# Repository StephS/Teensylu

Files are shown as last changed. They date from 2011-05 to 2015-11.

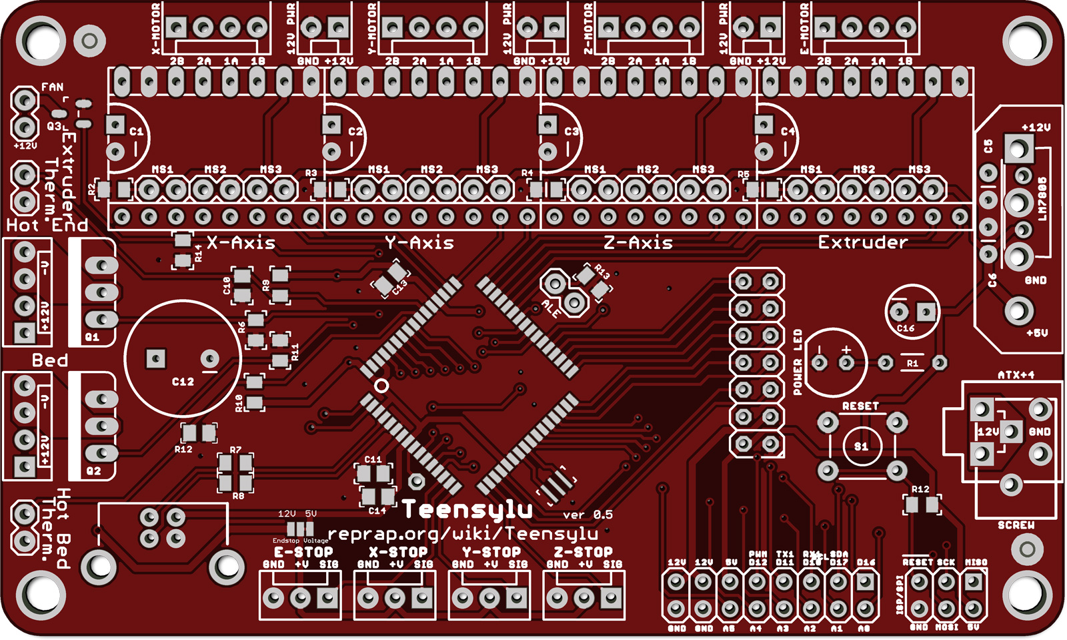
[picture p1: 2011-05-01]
teensylu-0.5/images/top.jpg

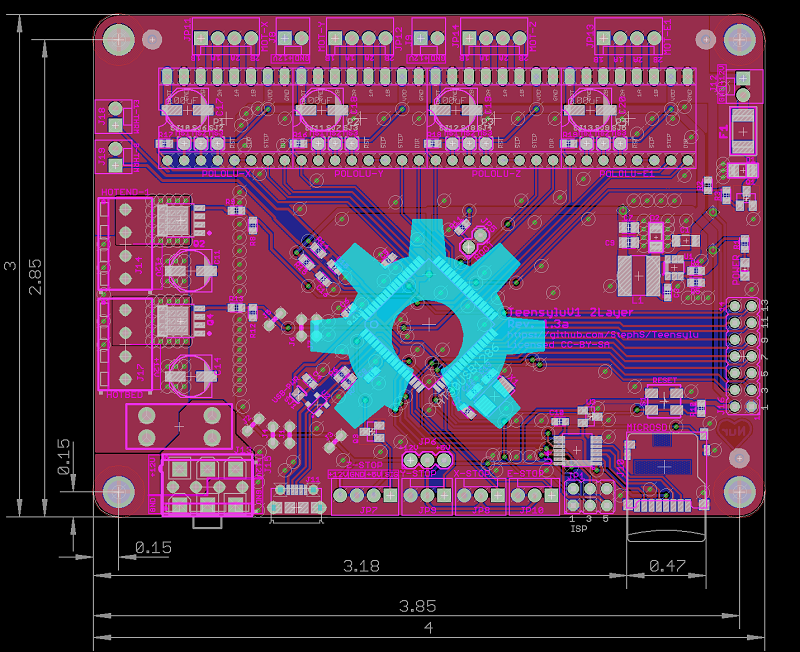
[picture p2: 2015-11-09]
TeensyluV1-2Layer/board.png

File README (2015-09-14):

UPDATE: TeensyluV1 is a complete redesign of the board. I have moved the power connector closer to the mosfets. Pins have changed! This new board is slightly larger than the older versions - It now matches the size of the Teensylu2
The hotend and bed connectors have changed to high power connectors. The main power connector can either be  screw connector, or a 6-Pin ATX-PCIE power connector. Please note the orientation of the connector and the polarity! Do not use the older 4 pin ATX connector!!!
It is highly recommended that this board is built using 2oz-in copper. Less than that may lead to board damage or FIRE!
I recommend a 15 Amp fuse in the mini-blade fuse holder.

I do not recommend using the older teensylu boards, get the TeensyluV1 board and use the added safety features.

I have decided to release 2 different versions of the board, The 2 Layer version, and 4 Layer version. The 4 layer version has greater power capacity due to uninterrupted power planes. The 2 layer version will be cheaper to manufacture. Functionally the boards are identical. I would prefer the 4 layer version, but I realize that COST is a major issue (up to 3 times the cost to manufacture 4 layer versus 2 layer).

As with all hobbiest electronics, there is a certain degree of risk involved. I had hoped that by making this project open source, that users would provide feedback and improvements to the design.
This has not happened.

Again, Use this board at your own risk!
I am releasing these designs without warranty or guarantee.

There is no such thing as a "Safe" 3d printer controller. Keep a smoke detector nearby and have a fire extinguisher handy. Do NOT the leave unattended. Disconnect from power source when not in use.

http://reprap.org/wiki/Teensylu

If you'd like to donate so I can buy the full version of Eagle, and make more cool stuff, please contact me through Google+ at https://plus.google.com/+StephanieS3D

Disclaimer:
These designs are provided without any warrenty, expressed or implied. This is a prototype designed for hobbiest use only.
Care should be taken during use and appropriate safety precautions taken.
The author is providing this item "as is". The author does not provide any warranty of the item whatsoever, whether express, implied, or statutory, including, but not limited to, any warranty of merchantability or fitness for a particular purpose or any warranty that the contents of the item will be error-free.
In no respect shall the author incur any liability for any damages, including, but limited to, direct, indirect, special, or consequential damages arising out of, resulting from, or any way connected to the use of the item, whether or not based upon warranty, contract, tort, or otherwise; whether or not injury was sustained by persons or property or otherwise; and whether or not loss was sustained from, or arose out of, the results of, the item, or any services that may be provided by the author.

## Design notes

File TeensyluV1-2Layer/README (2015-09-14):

Version 1.3 is ready for production, earlier versions should not be used.
This version is a 2 Layer board designed for low cost manufacturing. A 4 Layer board is also available.
It is required that the top and bottom layers be 2oz/in.
24v power supply should be possible, please note to use a 24v heat bed, hotend, and fans or else damage or FIRE can occur.

Assembly notes:
J1-J7 are 22ga Solid core wire jumpers at 0.1" spacing. Do not attempt to stuff with headers.
J13 and J15 occupy the same space. Choose an appropriate header for the target system.

Please see TeensyluV1_Pin_Mapping.txt for the correct pin mapping using the teensyduino library. Analog pins should use the analog pin reference.

The BOM is included. Please use parts of the same or higher ratings.

If you'd like to donate so I can buy the full version of Eagle, and make more cool stuff, please contact me through Google+ at https://plus.google.com/+StephanieS3D

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

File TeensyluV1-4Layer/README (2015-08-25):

Version 1.2 is ready for production, earlier versions should not be used.
This latest version of the board utilizes 4 layers. This is to improve the current capacity of the power planes.
It is recommended that the top and bottom layers be 2oz/in.
24v power supply should be possible, please note to use a 24v heat bed, hotend, and fans or else damage or FIRE can occur.

Please see TeensyluV1_Pin_Map.htm for the correct pin mapping using the teensyduino library. Analog pins should use the analog pin reference.

The BOM is included. Please use parts of the same or higher ratings.

If you'd like to donate so I can buy the full version of Eagle, and make more cool stuff, please contact me through Google+ at https://plus.google.com/+StephanieS3D

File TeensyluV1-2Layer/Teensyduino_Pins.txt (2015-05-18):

Pin #	PORT
0	PD0
1	PD1
2	PD2
3	PD3
4	PD4
5	PD5
6	PD6
7	PD7
8	PE0
9	PE1
10	PC0
11	PC1
12	PC2
13	PC3
14	PC4
15	PC5
16	PC6
17	PC7
18	PE6
19	PE7
20	PB0
21	PB1
22	PB2
23	PB3
24	PB4
25	PB5
26	PB6
27	PB7
28	PA0
29	PA1
30	PA2
31	PA3
32	PA4
33	PA5
34	PA6
35	PA7
36	PE4
37	PE5
38	PF0
39	PF1
40	PF2
41	PF3
42	PF4
43	PF5
44	PF6
45	PF7

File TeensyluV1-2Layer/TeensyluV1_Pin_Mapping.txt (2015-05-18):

Package Pin Number	Pin Name	Teensyduino Pin Number	Connected NET	Description
1	PE6	18	Z-STOP	Z Endstop or Z probe input
2	PE7	19	PE7	Not Connected
9	PE3		PE3	Not Connected
10	PB0	20	SDCS	SDCS
11	PB1	21	SCLK	SCLK
12	PB2	22	MOSI	MOSI
13	PB3	23	MISO	MISO
14	PB4	24	PB4	Extension Header PIN 5
15	PB5	25	Y-STOP	Y Endstop
16	PB6	26	X-STOP	X Endstop
17	PB7	27	SCDCD	SD Card Detect
18	PE4	36	E-STOP	E Endstop
19	PE5	37	PE5	Extension Header PIN 4
25	PD0	0	PD0-SCL	Extension Header PIN 6
26	PD1	1	PD1-SDA	Extension Header PIN 7
27	PD2	2	PD2-RX1	Extension Header PIN 8
28	PD3	3	PD3-TX1	Extension Header PIN 9
29	PD4	4	PD4	Extension Header PIN 10
30	PD5	5	PD5	Extension Header PIN 11
31	PD6	6	PD6	Extension Header PIN 12
32	PD7	7	PD7	Extension Header PIN 13
33	PE0	8	E2-STEP	Not Connected
34	PE1	9	E2-DIR	Not Connected
35	PC0	10	!E2-ENABLE	Not Connected
36	PC1	11	E1-DIR	1st Extruder STEP pin
37	PC2	12	E1-STEP	1st Extruder DIR pin
38	PC3	13	!E1-ENABLE	1st Extruder ENABLE pin
39	PC4	14	!HOTBED	Hot Bed Mosfet control pin
40	PC5	15	!HOTEND-1	Hot End 1 Mosfet control pin
41	PC6	16	!PWM-FAN	Fan Mosfet control pin
42	PC7	17	Z-DIR	Z Axis STEP pin
43	PE2		PE2	Boot Mode pin
44	PA7	35	Z-STEP	Z Axis DIR pin
45	PA6	34	!Z-ENABLE	Z Axis ENABLE pin
46	PA5	33	Y-DIR	Y Axis STEP pin
47	PA4	32	Y-STEP	Y Axis DIR pin
48	PA3	31	!Y-ENABLE	Y Axis ENABLE pin
49	PA2	30	X-DIR	X Axis STEP pin
50	PA1	29	X-STEP	X Axis DIR pin
51	PA0	28	!X-ENABLE	X Axis ENABLE pin
54	PF7	45	A7	Extension Header PIN 14
55	PF6	44	A6	Not Connected
56	PF5	43	A5	Not Connected
57	PF4	42	A4	Not Connected
58	PF3	41	!HOTEND-2	Not Connected
59	PF2	40	E2-THERM	Not Connected
60	PF1	39	E1-THERM	Hot End 1 thermistor input pin
61	PF0	38	B-THERM	Hot Bed thermistor input pin

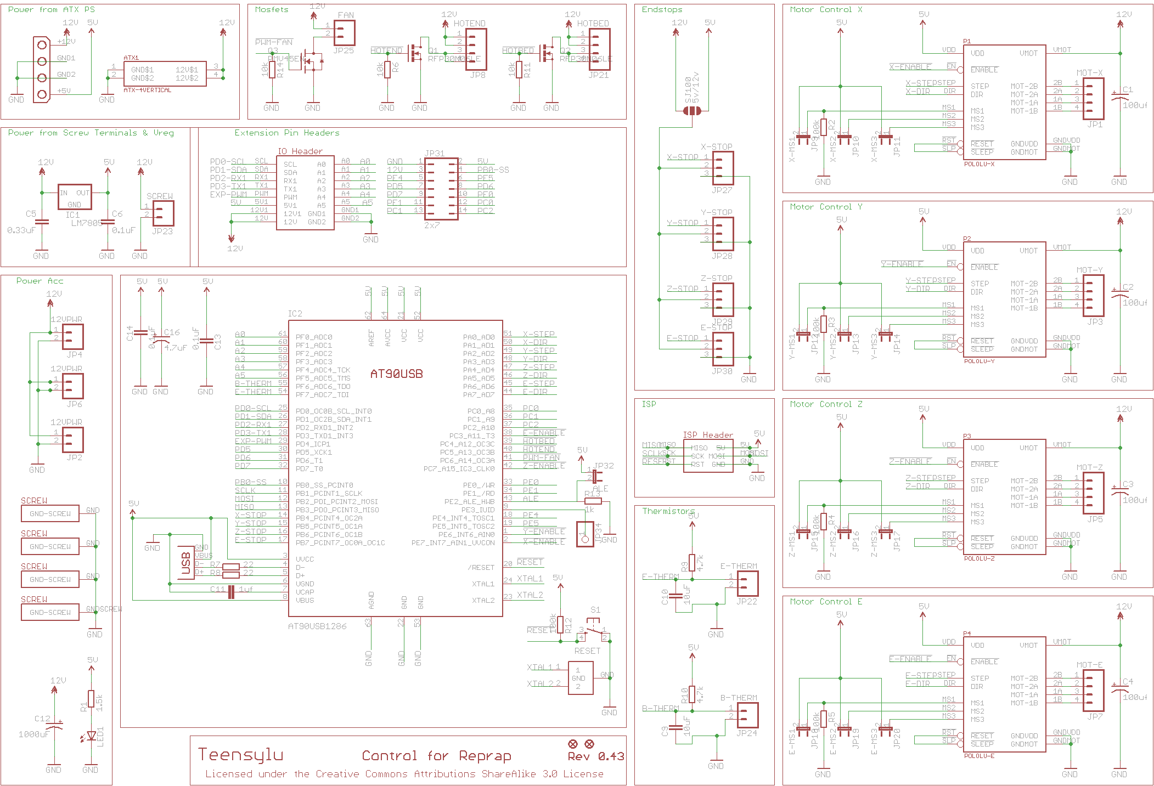
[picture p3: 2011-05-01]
teensylu-0.4.3/Schematic.png

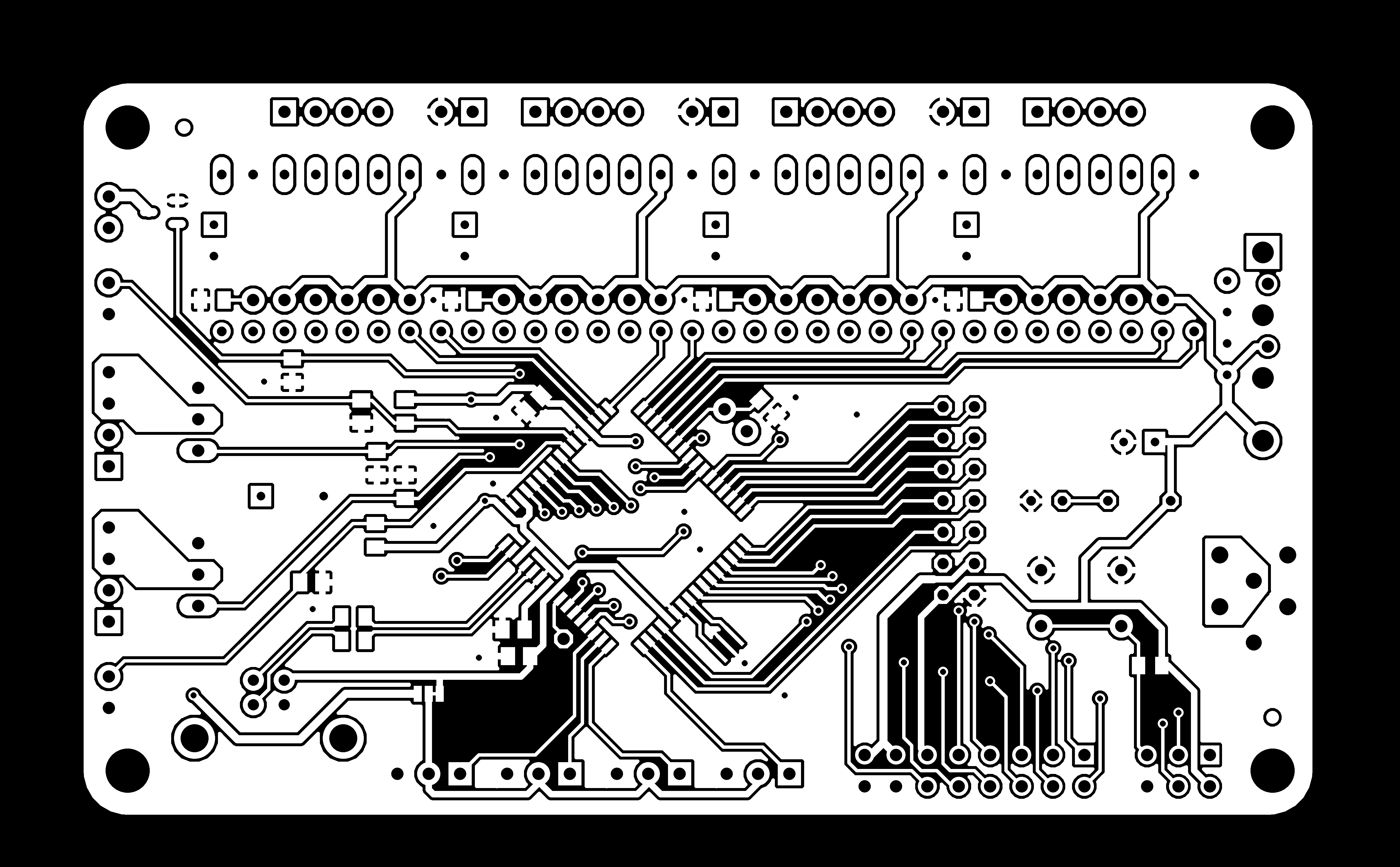
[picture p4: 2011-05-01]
teensylu-0.5/images/eagle_top.png

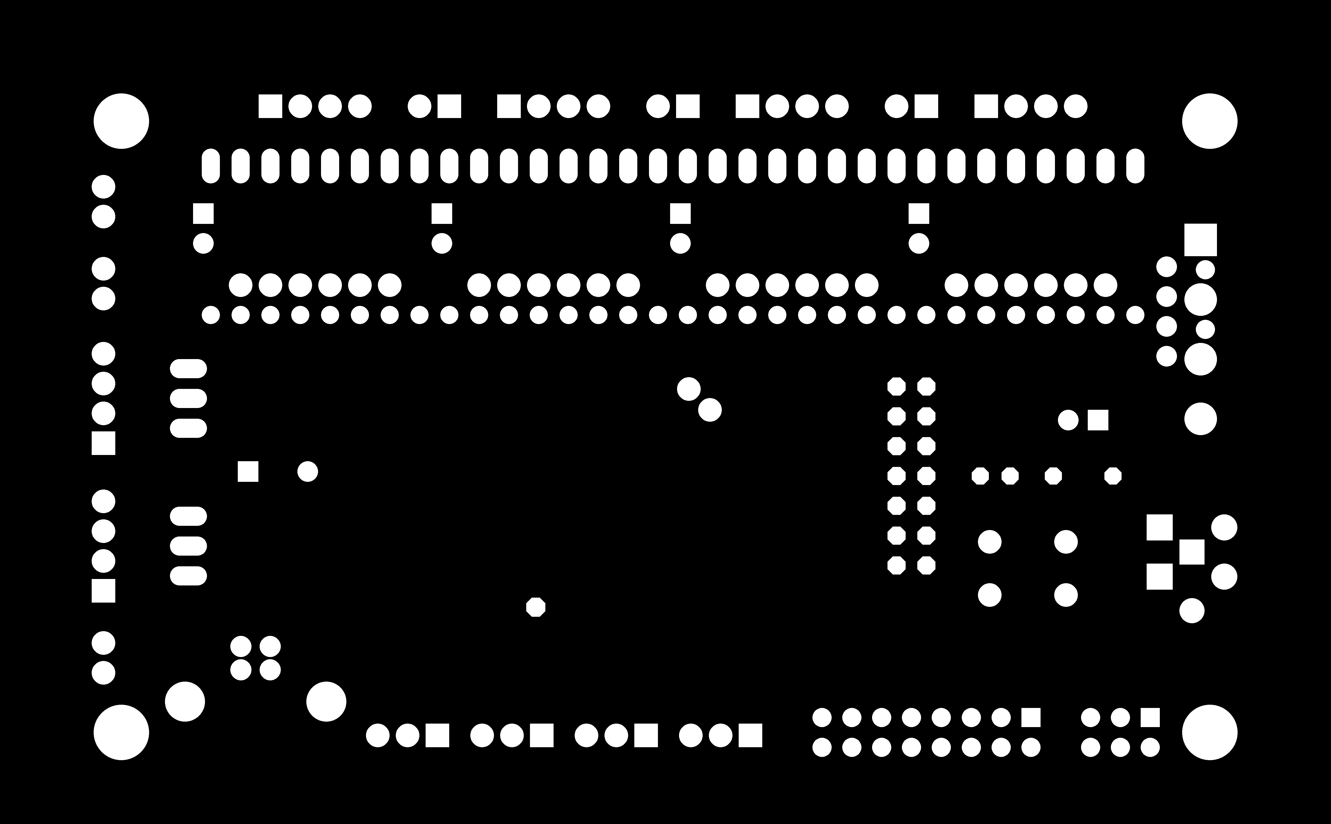
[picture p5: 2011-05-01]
teensylu-0.5/images/eagle_bottom_mask.png

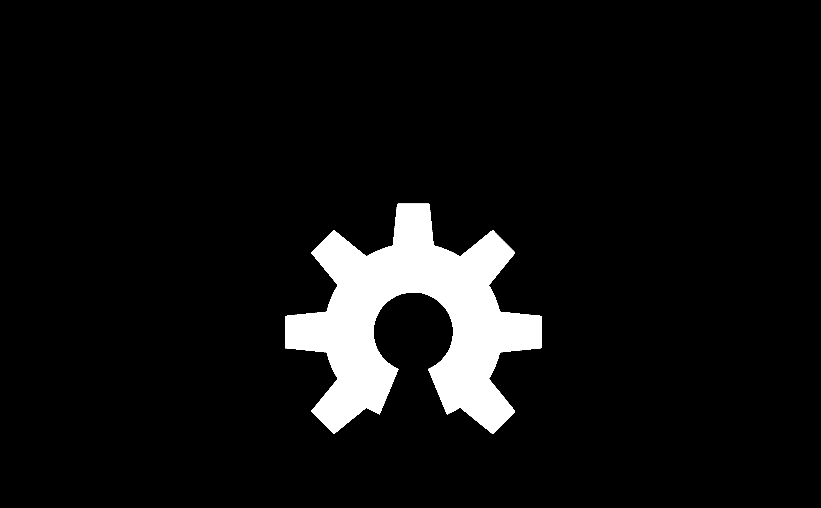
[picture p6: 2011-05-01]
teensylu-0.5/images/eagle_bottom_silk.png

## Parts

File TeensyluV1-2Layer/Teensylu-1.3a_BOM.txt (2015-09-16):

Part   Value                 Device                     Package             Description                                                                   CURRENT DCR   DESCRIPTION                               ESR    INDUCTANCE IRMS MANUFACTURER            MANUFACTURER_PART_NUMBER      NOTES                                                                       RDS_ON  REVERSE_VOLTAGE TOLERANCE VDC VGS   VOLTAGE VOLTAGE_OUTPUT
C1     4.7uF                 CAPACITOR_1206             CAPC3215X168N                                                                                                                                                                    Yaiyo Yuden             UMK316AB7475KL-T                                                                                                                  10%       50v                             
C2     0.1uF                 CAPACITOR_0603             CAPC1608X92N                                                                                                                                                                     Murata                  GRM188R71C104KA01D                                                                                                                10%       16V                             
C3     0.1uF                 CAPACITOR_0603             CAPC1608X92N                                                                                                                                                                     Samsung                 CL10B104KB8NNNC                                                                                                                   10%       50V                             
C4     0.1uF                 CAPACITOR_0603             CAPC1608X92N                                                                                                                                                                     Murata                  GRM188R71C104KA01D                                                                                                                10%       16V                             
C5     0.1uF                 CAPACITOR_0603             CAPC1608X92N                                                                                                                                                                     Murata                  GRM188R71C104KA01D                                                                                                                10%       16V                             
C6     0.1uF                 CAPACITOR_0603             CAPC1608X92N                                                                                                                                                                     Murata                  GRM188R71C104KA01D                                                                                                                10%       16V                             
C7     10uF                  CAPACITOR_0805             CAPC2012X145AN                                                                                                                                            0.0030                 Murata                  GRM21BR71A106KE51L                                                                                                                10%       10v                             
C8     1uF                   CAPACITOR_0603             CAPC1608X92N                                                                                                                                                                     Samsung                 CL10A105MO8NNNC                                                                                                                   20%       16V                             
C9     10uF                  CAPACITOR_0805             CAPC2012X145AN                                                                                                                                            0.0030                 Murata                  GRM21BR71A106KE51L                                                                                                                10%       10v                             
C10    10uF                  CAPACITOR_0603             CAPC1608X92N                                                                                                                                                                     Murata                  GRM188R61C106MA73D                                                                                                                20%       16V                             
C11    100uF                 CPOL-USD                   PANASONIC_D         POLARIZED CAPACITOR, American symbol                                                                                                                         Panasonic               EEE-FTH101XAP                                                                                                                     20%       50v                             
C12    10pF                  CAPACITOR_0603             CAPC1608X92N                                                                                                                                                                     Samsung                 CL10C100JB8NCNC                                                                                                                   5%        50V                             
C13    10pF                  CAPACITOR_0603             CAPC1608X92N                                                                                                                                                                     Samsung                 CL10C100JB8NCNC                                                                                                                   5%        50V                             
C14    100uF                 CPOL-USD                   PANASONIC_D         POLARIZED CAPACITOR, American symbol                                                                                                                         Panasonic               EEE-FTH101XAP                                                                                                                     20%       50v                             
C15    10uF                  CAPACITOR_0603             CAPC1608X92N                                                                                                                                                                     Murata                  GRM188R61C106MA73D                                                                                                                20%       16V                             
C16    10uF                  CAPACITOR_0603             CAPC1608X92N                                                                                                                                                                     Murata                  GRM188R61C106MA73D                                                                                                                20%       16V                             
C17    100uF                 CPOL-USD                   PANASONIC_D         POLARIZED CAPACITOR, American symbol                                                                                                                         Panasonic               EEE-FTH101XAP                                                                                                                     20%       50v                             
C18    100uF                 CPOL-USD                   PANASONIC_D         POLARIZED CAPACITOR, American symbol                                                                                                                         Panasonic               EEE-FTH101XAP                                                                                                                     20%       50v                             
C19    100uF                 CPOL-USD                   PANASONIC_D         POLARIZED CAPACITOR, American symbol                                                                                                                         Panasonic               EEE-FTH101XAP                                                                                                                     20%       50v                             
C20    100uF                 CPOL-USD                   PANASONIC_D         POLARIZED CAPACITOR, American symbol                                                                                                                         Panasonic               EEE-FTH101XAP                                                                                                                     20%       50v                             
D1     SCH-DIODESOD123F      SCH-DIODESOD123F           SOD123F             Schottky Diodes                                                               1A                                                                             NXP Semiconductors      PMEG4010CEH,115                                                                                                   40V                                                       
D2     SCH-DIODESOD123F      SCH-DIODESOD123F           SOD123F             Schottky Diodes                                                               1A                                                                             NXP Semiconductors      PMEG4010CEH,115                                                                                                   40V                                                       
F1     MINISMDC050F1812      MINISMDC050F1812           MINISMDC                                                                                          0.5A                                                                           TE Connectivity         MINISMDC050F-2                                                                                                                                                              
F2     MINI-FUSEMINI-FUSE    MINI-FUSEMINI-FUSE         MINI_FUSE                                                                                         15A                                                                            Keystone                3568                                                                                                                                                                        
J1     22ga                  WIRE_JUMPER-0.1            WJ_01_08            A wire jumper.  This component lets you give the same net two different names               22ga jumper wire                                                 N/A                     N/A                                                                                                                                                                         
J2     22ga                  WIRE_JUMPER-0.1            WJ_01_08            A wire jumper.  This component lets you give the same net two different names               22ga jumper wire                                                 N/A                     N/A                                                                                                                                                                         
J3     22ga                  WIRE_JUMPER-0.1            WJ_01_08            A wire jumper.  This component lets you give the same net two different names               22ga jumper wire                                                 N/A                     N/A                                                                                                                                                                         
J4     22ga                  WIRE_JUMPER-0.1            WJ_01_08            A wire jumper.  This component lets you give the same net two different names               22ga jumper wire                                                 N/A                     N/A                                                                                                                                                                         
J5     22ga                  WIRE_JUMPER-0.1            WJ_01_08            A wire jumper.  This component lets you give the same net two different names               22ga jumper wire                                                 N/A                     N/A                                                                                                                                                                         
J6     22ga                  WIRE_JUMPER-0.1            WJ_01_08            A wire jumper.  This component lets you give the same net two different names               22ga jumper wire                                                 N/A                     N/A                                                                                                                                                                         
J7     22ga                  WIRE_JUMPER-0.1            WJ_01_08            A wire jumper.  This component lets you give the same net two different names               22ga jumper wire                                                 N/A                     N/A                                                                                                                                                                         
J8     M02POLAR              M02POLAR                   MOLEX-1X2           Header 2                                                                                    CONN HEADER 2POS .100 VERT TIN                                   Molex                   0022272021                    Can use alternative part for Right Angle. MFG: TE Connectivity PN: 640455-2                                                                   
J9     M02POLAR              M02POLAR                   MOLEX-1X2           Header 2                                                                                    CONN HEADER 2POS .100 VERT TIN                                   Molex                   0022272021                    Can use alternative part for Right Angle. MFG: TE Connectivity PN: 640455-2                                                                   
J10    MICROSD               MICROSD                    AMPHENOL-MICROSD                                                                                                CONN MICRO SD CARD PUSH-PULL R/A                                 Amphenol                114-00841-68                                                                                                                                                                
J11    USB-MICRO-PTH         USB-MICRO-PTH              USB-MICROB-PTH      USB Connectors                                                                                                                                               FCI                     10118194-0001LF                                                                                                                                                             
J12    M02POLAR              M02POLAR                   MOLEX-1X2           Header 2                                                                                    CONN HEADER 2POS .100 VERT TIN                                   Molex                   0022272021                    Can use alternative part for Right Angle. MFG: TE Connectivity PN: 640455-2                                                                   
J13    4P-TERM-BLOCK284391-4 4P-TERM-BLOCK284391-4      284391-4                                                                                          12A                                                                            TE Connectivity         284391-4                                                                                                                                                                    
J14    HOTEND-1              4P-TERM-BLOCK284391-4      284391-4                                                                                          12A                                                                            TE Connectivity         284391-4                                                                                                                                                                    
J15    39-29-3066            39-29-3066                 39-29-3066          Mini FIT connector 6 pol Without Snap-in peg                                                                                                                 Molex                   0039293066                                                                                                                                                                  
J16    2x7                   JP7Q                       JP7Q                JUMPER                                                                                      DIL VERTICAL PC TAIL PIN HEADER                                  Harwin                  M20-9980746                                                                                                                                                                 
J17    HOTBED                4P-TERM-BLOCK284391-4      284391-4                                                                                          12A                                                                            TE Connectivity         284391-4                                                                                                                                                                    
J18    M02POLAR              M02POLAR                   MOLEX-1X2           Header 2                                                                                    CONN HEADER 2POS .100 VERT TIN                                   Molex                   0022272021                    Can use alternative part for Right Angle. MFG: TE Connectivity PN: 640455-2                                                                   
J19    M02POLAR              M02POLAR                   MOLEX-1X2           Header 2                                                                                    CONN HEADER 2POS .100 VERT TIN                                   Molex                   0022272021                    Can use alternative part for Right Angle. MFG: TE Connectivity PN: 640455-2                                                                   
JP1    ISP                   PROGHEADER                 ISP                 JUMPER                                                                                                                                                                                                                                                                                                                                                           
JP2    FIDUCIAL1X2.5         FIDUCIAL1X2.5              FIDUCIAL-1X2.5      Fiducial Alignment Points                                                                                                                                                                                                                                                                                                                                        
JP3    FIDUCIAL1X2.5         FIDUCIAL1X2.5              FIDUCIAL-1X2.5      Fiducial Alignment Points                                                                                                                                                                                                                                                                                                                                        
JP4    FIDUCIAL1X2.5         FIDUCIAL1X2.5              FIDUCIAL-1X2.5      Fiducial Alignment Points                                                                                                                                                                                                                                                                                                                                        
JP5    BOOT                  JUMPER-2PTH                1X02                Jumper                                                                                      SIL VERTICAL PC TAIL PIN HEADER                                  Harwin                  M20-9990246                                                                                                                                                                 
JP6    JUMPER-3PTH           JUMPER-3PTH                1X03                                                                                                                                                                                                                                                                                                                                                                                 
JP7    Z-STOP                M04POLAR                   MOLEX-1X4           Header 4                                                                                    CONN HEADER 4POS .100 VERT TIN                                   Molex                   0022272041                    Can use alternative part for Right Angle. MFG: TE Connectivity PN: 640455-4                                                                   
JP8    M03POLAR              M03POLAR                   MOLEX-1X3           Header 3                                                                                    CONN HEADER 3POS .100 VERT TIN                                   Molex                   0022272031                    Can use alternative part for Right Angle. MFG: TE Connectivity PN: 640455-3                                                                   
JP9    M03POLAR              M03POLAR                   MOLEX-1X3           Header 3                                                                                    CONN HEADER 3POS .100 VERT TIN                                   Molex                   0022272031                    Can use alternative part for Right Angle. MFG: TE Connectivity PN: 640455-3                                                                   
JP10   M03POLAR              M03POLAR                   MOLEX-1X3           Header 3                                                                                    CONN HEADER 3POS .100 VERT TIN                                   Molex                   0022272031                    Can use alternative part for Right Angle. MFG: TE Connectivity PN: 640455-3                                                                   
JP11   MOT-X                 M04POLAR                   MOLEX-1X4           Header 4                                                                                    CONN HEADER 4POS .100 VERT TIN                                   Molex                   0022272041                    Can use alternative part for Right Angle. MFG: TE Connectivity PN: 640455-4                                                                   
JP12   MOT-Y                 M04POLAR                   MOLEX-1X4           Header 4                                                                                    CONN HEADER 4POS .100 VERT TIN                                   Molex                   0022272041                    Can use alternative part for Right Angle. MFG: TE Connectivity PN: 640455-4                                                                   
JP13   MOT-E1                M04POLAR                   MOLEX-1X4           Header 4                                                                                    CONN HEADER 4POS .100 VERT TIN                                   Molex                   0022272041                    Can use alternative part for Right Angle. MFG: TE Connectivity PN: 640455-4                                                                   
JP14   MOT-Z                 M04POLAR                   MOLEX-1X4           Header 4                                                                                    CONN HEADER 4POS .100 VERT TIN                                   Molex                   0022272041                    Can use alternative part for Right Angle. MFG: TE Connectivity PN: 640455-4                                                                   
L1     68uH                  INDUCTORSRN6045            SRN6045                                                                                           900mA   0.351                                                  68uH       0.9A Bourns                  SRN6045-680M                                                                                                                                                                
LED1   POWER                 LEDCHIPLED_0805            CHIPLED_0805        LED                                                                                                                                                          Kingbright              APT2012SGC                                                                                                                                                                  
P1     POLOLU-X              POLOLU-ALLEGRO             POLOLU-STEPPER-PTH                                                                                                                                                                                                                                                                                                                                                                   
P2     POLOLU-Y              POLOLU-ALLEGRO             POLOLU-STEPPER-PTH                                                                                                                                                                                                                                                                                                                                                                   
P3     POLOLU-Z              POLOLU-ALLEGRO             POLOLU-STEPPER-PTH                                                                                                                                                                                                                                                                                                                                                                   
P4     POLOLU-E1             POLOLU-ALLEGRO             POLOLU-STEPPER-PTH                                                                                                                                                                                                                                                                                                                                                                   
Q1     PMV45EN               MOSFET-NCH_SOT-23          SOT23C                                                                                            1.2A                                                                           International Rectifier IRLML2060TRPBF                                                                                                                                        60V                   
Q2     PSMN1R8-40YLC         PSMN1R8-40YLCPOWERPACK-S08 LFPACK-POWERPAK-SO8 N-Channel MOSFET - 40V 100A LFPAK                                             100A                                                                           NXP Semiconductors      PSMN1R8-40YLC,115                                                                                         1.8mOhm                               1.95V 40V                   
Q3     MMUN2211LT3G          TRANSISTOR_NPN_BIASSOT23C  SOT23C              Transistor NPN                                                                              TRANS PREBIAS NPN 246MW SOT23-3                                  ON Semiconductor        MMUN2211LT3G                                                                                                                                                                
Q4     PSMN1R8-40YLC         PSMN1R8-40YLCPOWERPACK-S08 LFPACK-POWERPAK-SO8 N-Channel MOSFET - 40V 100A LFPAK                                             100A                                                                           NXP Semiconductors      PSMN1R8-40YLC,115                                                                                         1.8mOhm                               1.95V 40V                   
R1     1K                    RESISTOR_0603              RESC1608X55N
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

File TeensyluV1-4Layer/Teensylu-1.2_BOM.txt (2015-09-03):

Part   Value                 Device                     Package             Description                                  CURRENT DCR   DESCRIPTION                      ESR    INDUCTANCE IRMS MANUFACTURER            MANUFACTURER_PART_NUMBER      NOTES                                                                       RDS_ON   REVERSE_VOLTAGE TOLERANCE VDC VGS   VOLTAGE VOLTAGE_OUTPUT
C1     4.7uF                 CAPACITOR_1206             CAPC3215X168N                                                                                                                          Yaiyo Yuden             UMK316AB7475KL-T                                                                                                                   10%       50v                             
C2     100uF                 CPOL-USD                   PANASONIC_D         POLARIZED CAPACITOR, American symbol                                                                               Panasonic               EEE-FTH101XAP                                                                                                                      20%       50v                             
C3     0.1uF                 CAPACITOR_0603             CAPC1608X92N                                                                                                                           Murata                  GRM188R71C104KA01D                                                                                                                 10%       16V                             
C4     0.1uF                 CAPACITOR_0603             CAPC1608X92N                                                                                                                           Samsung                 CL10B104KB8NNNC                                                                                                                    10%       50V                             
C5     0.1uF                 CAPACITOR_0603             CAPC1608X92N                                                                                                                           Murata                  GRM188R71C104KA01D                                                                                                                 10%       16V                             
C6     0.1uF                 CAPACITOR_0603             CAPC1608X92N                                                                                                                           Murata                  GRM188R71C104KA01D                                                                                                                 10%       16V                             
C7     0.1uF                 CAPACITOR_0603             CAPC1608X92N                                                                                                                           Murata                  GRM188R71C104KA01D                                                                                                                 10%       16V                             
C8     10uF                  CAPACITOR_0805             CAPC2012X145AN                                                                                                  0.0030                 Murata                  GRM21BR71A106KE51L                                                                                                                 10%       10v                             
C9     1uF                   CAPACITOR_0603             CAPC1608X92N                                                                                                                           Samsung                 CL10A105MO8NNNC                                                                                                                    20%       16V                             
C10    10uF                  CAPACITOR_0805             CAPC2012X145AN                                                                                                  0.0030                 Murata                  GRM21BR71A106KE51L                                                                                                                 10%       10v                             
C11    10uF                  CAPACITOR_0603             CAPC1608X92N                                                                                                                           Murata                  GRM188R61C106MA73D                                                                                                                 20%       16V                             
C12    10pF                  CAPACITOR_0603             CAPC1608X92N                                                                                                                           Samsung                 CL10C100JB8NCNC                                                                                                                    5%        50V                             
C13    10pF                  CAPACITOR_0603             CAPC1608X92N                                                                                                                           Samsung                 CL10C100JB8NCNC                                                                                                                    5%        50V                             
C14    10uF                  CAPACITOR_0603             CAPC1608X92N                                                                                                                           Murata                  GRM188R61C106MA73D                                                                                                                 20%       16V                             
C15    10uF                  CAPACITOR_0603             CAPC1608X92N                                                                                                                           Murata                  GRM188R61C106MA73D                                                                                                                 20%       16V                             
C17    100uF                 CPOL-USD                   PANASONIC_D         POLARIZED CAPACITOR, American symbol                                                                               Panasonic               EEE-FTH101XAP                                                                                                                      20%       50v                             
C18    100uF                 CPOL-USD                   PANASONIC_D         POLARIZED CAPACITOR, American symbol                                                                               Panasonic               EEE-FTH101XAP                                                                                                                      20%       50v                             
C19    100uF                 CPOL-USD                   PANASONIC_D         POLARIZED CAPACITOR, American symbol                                                                               Panasonic               EEE-FTH101XAP                                                                                                                      20%       50v                             
C20    100uF                 CPOL-USD                   PANASONIC_D         POLARIZED CAPACITOR, American symbol                                                                               Panasonic               EEE-FTH101XAP                                                                                                                      20%       50v                             
D1     SCH-DIODESOD123F      SCH-DIODESOD123F           SOD123F             Schottky Diodes                              1A                                                                    NXP Semiconductors      PMEG4010CEH,115                                                                                                    40V                                                       
D2     SCH-DIODESOD123F      SCH-DIODESOD123F           SOD123F             Schottky Diodes                              1A                                                                    NXP Semiconductors      PMEG4010CEH,115                                                                                                    40V                                                       
F1     MINISMDC050F1812      MINISMDC050F1812           MINISMDC                                                         0.5A                                                                  TE Connectivity         MINISMDC050F-2                                                                                                                                                               
F2     MINI-FUSEMINI-FUSE    MINI-FUSEMINI-FUSE         MINI_FUSE                                                        15A                                                                   Keystone                3568                                                                                                                                                                         
J1     M02POLAR              M02POLAR                   MOLEX-1X2           Header 2                                                   CONN HEADER 2POS .100 VERT TIN                          Molex                   0022272021                    Can use alternative part for Right Angle. MFG: TE Connectivity PN: 640455-2                                                                    
J2     MICROSD               MICROSD                    AMPHENOL-MICROSD                                                               CONN MICRO SD CARD PUSH-PULL R/A                        Amphenol                114-00841-68                                                                                                                                                                 
J3     USB-MICRO-PTH         USB-MICRO-PTH              USB-MICROB-PTH      USB Connectors                                                                                                     FCI                     10118194-0001LF                                                                                                                                                              
J4     M02POLAR              M02POLAR                   MOLEX-1X2           Header 2                                                   CONN HEADER 2POS .100 VERT TIN                          Molex                   0022272021                    Can use alternative part for Right Angle. MFG: TE Connectivity PN: 640455-2                                                                    
J5     4P-TERM-BLOCK284391-4 4P-TERM-BLOCK284391-4      284391-4                                                         12A                                                                   TE Connectivity         284391-4                                                                                                                                                                     
J6     39-29-3066            39-29-3066                 39-29-3066          Mini FIT connector 6 pol Without Snap-in peg                                                                       Molex                   0039293066                                                                                                                                                                   
J7     HOTEND-1              4P-TERM-BLOCK284391-4      284391-4                                                         12A                                                                   TE Connectivity         284391-4                                                                                                                                                                     
J8     2x7                   JP7Q                       JP7Q                JUMPER                                                     DIL VERTICAL PC TAIL PIN HEADER                         Harwin                  M20-9980746                                                                                                                                                                  
J9     HOTBED                4P-TERM-BLOCK284391-4      284391-4                                                         12A                                                                   TE Connectivity         284391-4                                                                                                                                                                     
J11    M02POLAR              M02POLAR                   MOLEX-1X2           Header 2                                                   CONN HEADER 2POS .100 VERT TIN                          Molex                   0022272021                    Can use alternative part for Right Angle. MFG: TE Connectivity PN: 640455-2                                                                    
J12    M02POLAR              M02POLAR                   MOLEX-1X2           Header 2                                                   CONN HEADER 2POS .100 VERT TIN                          Molex                   0022272021                    Can use alternative part for Right Angle. MFG: TE Connectivity PN: 640455-2                                                                    
JP1    FIDUCIAL1X2.5         FIDUCIAL1X2.5              FIDUCIAL-1X2.5      Fiducial Alignment Points                                                                                                                                                                                                                                                                                               
JP2    FIDUCIAL1X2.5         FIDUCIAL1X2.5              FIDUCIAL-1X2.5      Fiducial Alignment Points                                                                                                                                                                                                                                                                                               
JP3    BOOT                  JUMPER-2PTH                1X02                Jumper                                                     SIL VERTICAL PC TAIL PIN HEADER                         Harwin                  M20-9990246                                                                                                                                                                  
JP4    JUMPER-3PTH           JUMPER-3PTH                1X03                                                                                                                                                                                                                                                                                                                                        
JP5    ISP                   PROGHEADER                 ISP                 JUMPER                                                                                                                                                                                                                                                                                                                  
JP6    JUMPER-3PTH           JUMPER-3PTH                1X03                                                                                                                                                                                                                                                                                                                                        
JP7    M03POLAR              M03POLAR                   MOLEX-1X3           Header 3                                                   CONN HEADER 3POS .100 VERT TIN                          Molex                   0022272031                    Can use alternative part for Right Angle. MFG: TE Connectivity PN: 640455-3                                                                    
JP8    M03POLAR              M03POLAR                   MOLEX-1X3           Header 3                                                   CONN HEADER 3POS .100 VERT TIN                          Molex                   0022272031                    Can use alternative part for Right Angle. MFG: TE Connectivity PN: 640455-3                                                                    
JP9    M03POLAR              M03POLAR                   MOLEX-1X3           Header 3                                                   CONN HEADER 3POS .100 VERT TIN                          Molex                   0022272031                    Can use alternative part for Right Angle. MFG: TE Connectivity PN: 640455-3                                                                    
JP10   M03POLAR              M03POLAR                   MOLEX-1X3           Header 3                                                   CONN HEADER 3POS .100 VERT TIN                          Molex                   0022272031                    Can use alternative part for Right Angle. MFG: TE Connectivity PN: 640455-3                                                                    
JP11   MOT-X                 M04POLAR                   MOLEX-1X4           Header 4                                                   CONN HEADER 4POS .100 VERT TIN                          Molex                   0022272041                    Can use alternative part for Right Angle. MFG: TE Connectivity PN: 640455-4                                                                    
JP12   MOT-Y                 M04POLAR                   MOLEX-1X4           Header 4                                                   CONN HEADER 4POS .100 VERT TIN                          Molex                   0022272041                    Can use alternative part for Right Angle. MFG: TE Connectivity PN: 640455-4                                                                    
JP13   MOT-E1                M04POLAR                   MOLEX-1X4           Header 4                                                   CONN HEADER 4POS .100 VERT TIN                          Molex                   0022272041                    Can use alternative part for Right Angle. MFG: TE Connectivity PN: 640455-4
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

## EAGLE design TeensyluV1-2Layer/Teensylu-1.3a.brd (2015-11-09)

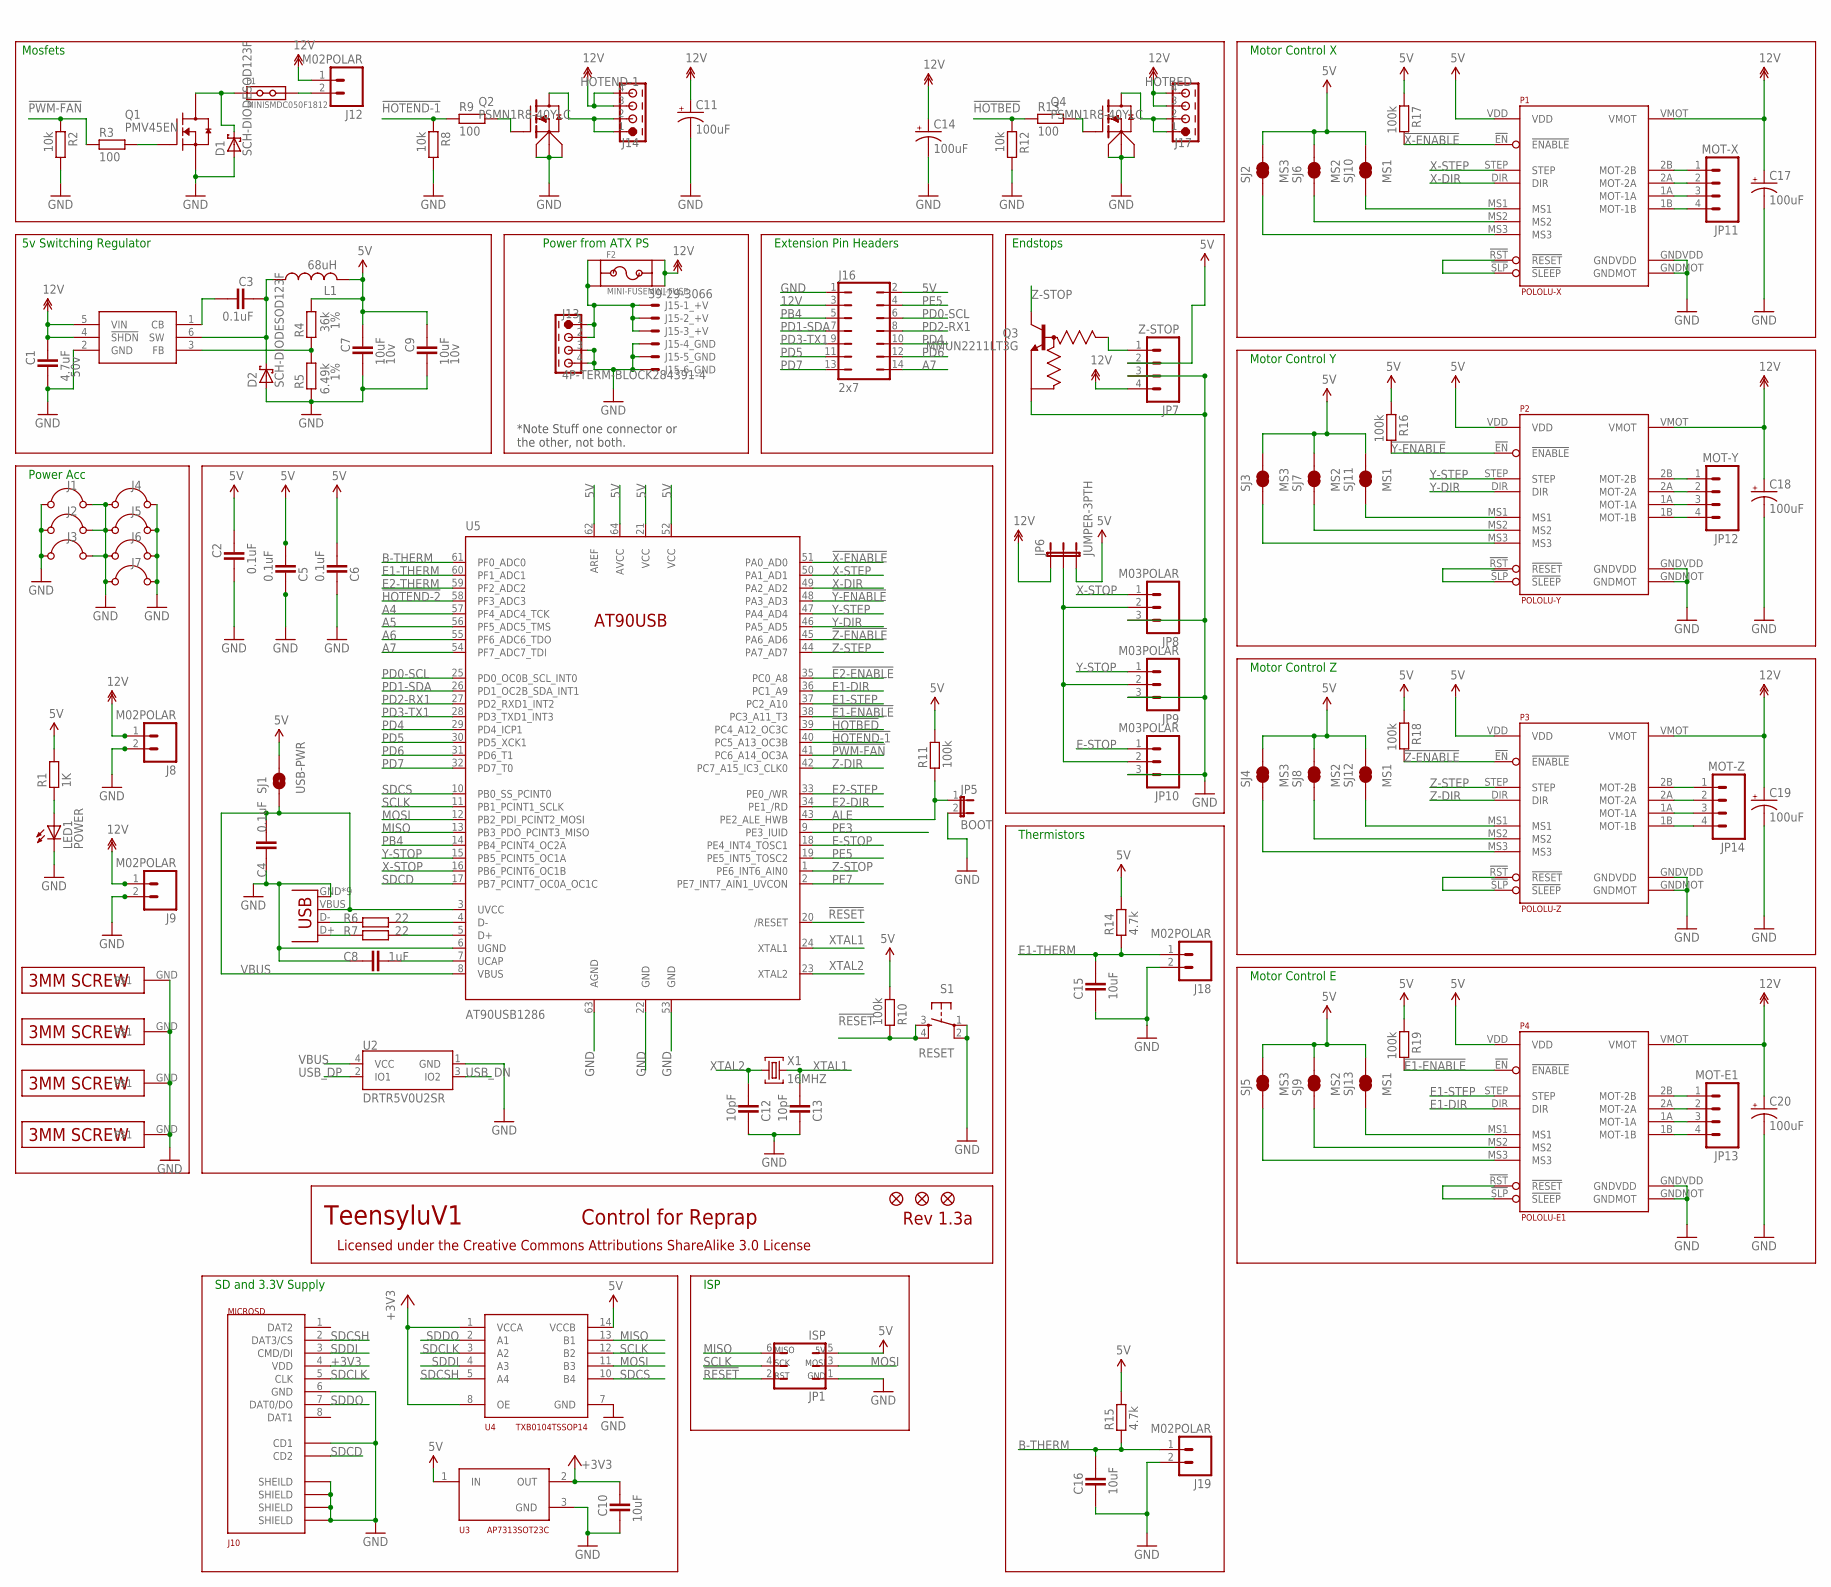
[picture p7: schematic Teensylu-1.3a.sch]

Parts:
C1: 4.7uF; CAPC3215X168N; TOLERANCE 10%; MANUFACTURER_PART_NUMBER UMK316AB7475KL-T
C2, C4, C5, C6: 0.1uF; CAPC1608X92N; TOLERANCE 10%; MANUFACTURER_PART_NUMBER GRM188R71C104KA01D
C3: 0.1uF; CAPC1608X92N; TOLERANCE 10%; MANUFACTURER_PART_NUMBER CL10B104KB8NNNC
C7, C9: 10uF; CAPC2012X145AN; TOLERANCE 10%; MANUFACTURER_PART_NUMBER GRM21BR71A106KE51L
C8: 1uF; CAPC1608X92N; TOLERANCE 20%; MANUFACTURER_PART_NUMBER CL10A105MO8NNNC
C10, C15, C16: 10uF; CAPC1608X92N; TOLERANCE 20%; MANUFACTURER_PART_NUMBER GRM188R61C106MA73D
C11, C14, C17, C18, C19, C20: 100uF; PANASONIC_D; TOLERANCE 20%; MANUFACTURER_PART_NUMBER EEE-FTH101XAP
C12, C13: 10pF; CAPC1608X92N; TOLERANCE 5%; MANUFACTURER_PART_NUMBER CL10C100JB8NCNC
D1: SCH-DIODESOD123F; SOD123F
D2: SCH-DIODESOD123F; SOD123F; MANUFACTURER_PART_NUMBER PMEG4010CEH,115
F1: MINISMDC050F1812; MINISMDC
F2: MINI-FUSEMINI-FUSE; MINI_FUSE
J1, J2, J3, J4, J5, J6, J7: 22ga; WJ_01_08; MANUFACTURER_PART_NUMBER N/A
J8, J9, J12, J18, J19: M02POLAR; MOLEX-1X2; MANUFACTURER_PART_NUMBER 0022272021
J10: MICROSD; AMPHENOL-MICROSD
J11: USB-MICRO-PTH; USB-MICROB-PTH
J13: 4P-TERM-BLOCK284391-4; 284391-4
J14: HOTEND-1; 284391-4
J15: 39-29-3066
J16: 2x7; JP7Q; MANUFACTURER_PART_NUMBER M20-9980746
J17: HOTBED; 284391-4
JP1: ISP
JP2, JP3, JP4: FIDUCIAL1X2.5; FIDUCIAL-1X2.5
JP5: BOOT; 1X02; MANUFACTURER_PART_NUMBER M20-9990246
JP6: JUMPER-3PTH; 1X03
JP7: Z-STOP; MOLEX-1X4
JP8, JP9, JP10: M03POLAR; MOLEX-1X3; MANUFACTURER_PART_NUMBER 0022272031
JP11: MOT-X; MOLEX-1X4
JP12: MOT-Y; MOLEX-1X4
JP13: MOT-E1; MOLEX-1X4
JP14: MOT-Z; MOLEX-1X4
L1: 68uH; SRN6045; MANUFACTURER_PART_NUMBER SRN6045-680M
LED1: POWER; CHIPLED_0805; MANUFACTURER_PART_NUMBER APT2012SGC
P1: POLOLU-X; POLOLU-STEPPER-PTH
P2: POLOLU-Y; POLOLU-STEPPER-PTH
P3: POLOLU-Z; POLOLU-STEPPER-PTH
P4: POLOLU-E1; POLOLU-STEPPER-PTH
Q1: PMV45EN; SOT23C; VOLTAGE 60V; MANUFACTURER_PART_NUMBER IRLML2060TRPBF
Q2, Q4: PSMN1R8-40YLC; LFPACK-POWERPAK-SO8
Q3: MMUN2211LT3G; SOT23C; MANUFACTURER_PART_NUMBER MMUN2211LT3G
R1: 1K; RESC1608X55N
R2, R8, R12: 10k; RESC1608X55N
R3, R9, R13: 100; RESC1608X55N
R4: 36k; RESC1608X55N; TOLERANCE 1%
R5: 6.49k; RESC1608X55N; TOLERANCE 1%
R6, R7: 22; RESC1608X55N
R10, R11, R16, R17, R18, R19: 100k; RESC1608X55N
R14, R15: 4.7k; RESC1608X55N
S1: RESET; TACTILE_SWITCH_SMD
SCREW1, SCREW2, SCREW3, SCREW4: 3MM-SCREW; PLATEDSCREW
SJ1: USB-PWR; SJ_2S-NO
SJ2, SJ3, SJ4, SJ5: MS3; SJ_2S-TRACE
SJ6, SJ7, SJ8, SJ9: MS2; SJ_2S-TRACE
SJ10, SJ11, SJ12, SJ13: MS1; SJ_2S-TRACE
U1: LMR16006X; TSOT6
U2: DRTR5V0U2SR; SOT143-R
U3: AP7313SOT23C; SOT23C
U4: TXB0104TSSOP14; TSSOP14
U5: AT90USB1286; TQFP64-2; MANUFACTURER_PART_NUMBER AT90USB1286
X1: 16MHZ; NDK-XTAL; MANUFACTURER_PART_NUMBER NX5032GA-16.000000MHZ-LN-CD-1

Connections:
5V: C2.1, C5.2, C6.2, C7.1, C9.1, J16.2, JP1.5, JP6.3, JP7.2, L1.2, P1.VDD, P2.VDD, P3.VDD, P4.VDD, R1.2, R4.1, R10.2, R11.2, R14.2, R15.2, R16.1, R17.1, R18.1, R19.1, SJ1.2, SJ2.2, SJ3.2, SJ4.2, SJ5.2, SJ6.2, SJ7.2, SJ8.2, SJ9.2, SJ10.2, SJ11.2, SJ12.2, SJ13.2, U3.1 (IN), U4.14 (VCCB), U5.21 (VCC), U5.52 (VCC), U5.62 (AREF), U5.64 (AVCC)
5VREG_CB: C3.2, U1.1 (CB)
5VREG_FB: R4.2, R5.1, U1.3 (FB)
5VREG_SW: C3.1, D2.C, L1.1, U1.6 (SW)
12V: C1.1, C11.+, C14.+, C17.+, C18.+, C19.+, C20.+, F2.P$3, F2.P$4, J8.1, J9.1, J12.1, J14.3, J14.4, J16.3, J17.3, J17.4, JP6.1, JP7.4, P1.VMOT, P2.VMOT, P3.VMOT, P4.VMOT, U1.4 (!SHDN), U1.5 (VIN)
12V_FUSE: F2.P$1, F2.P$2, J13.1, J13.2, J15.1, J15.2, J15.3
!E1-ENABLE: P4.!EN (!ENABLE), R19.2, U5.38 (PC3_A11_T3)
!E2-ENABLE: U5.35 (PC0_A8)
!HOTBED: R12.1, R13.1, U5.39 (PC4_A12_OC3C)
!HOTEND-1: R8.1, R9.1, U5.40 (PC5_A13_OC3B)
!HOTEND-2: U5.58 (PF3_ADC3)
!PWM-FAN: R2.1, R3.1, U5.41 (PC6_A14_OC3A)
!RESET: JP1.2, R10.1, S1.3, S1.4, U5.20 (/RESET)
!X-ENABLE: P1.!EN (!ENABLE), R17.2, U5.51 (PA0_AD0)
!Y-ENABLE: P2.!EN (!ENABLE), R16.2, U5.48 (PA3_AD3)
!Z-ENABLE: P3.!EN (!ENABLE), R18.2, U5.45 (PA6_AD6)
+3V3: C10.1, J10.4 (VDD), U3.2 (OUT), U4.1 (VCCA), U4.8 (OE)
A4: U5.57 (PF4_ADC4_TCK)
A5: U5.56 (PF5_ADC5_TMS)
A6: U5.55 (PF6_ADC6_TDO)
A7: J16.14, U5.54 (PF7_ADC7_TDI)
ALE: JP5.1, R11.1, U5.43 (PE2_ALE_HWB)
B-THERM: C16.2, J19.1, R15.1, U5.61 (PF0_ADC0)
E1-DIR: P4.DIR, U5.36 (PC1_A9)
E1-STEP: P4.STEP, U5.37 (PC2_A10)
E1-THERM: C15.2, J18.1, R14.1, U5.60 (PF1_ADC1)
E2-DIR: U5.34 (PE1_/RD)
E2-STEP: U5.33 (PE0_/WR)
E2-THERM: U5.59 (PF2_ADC2)
E-MOT-1A: JP13.3, P4.1A (MOT-1A)
E-MOT-1B: JP13.4, P4.1B (MOT-1B)
E-MOT-2A: JP13.2, P4.2A (MOT-2A)
E-MOT-2B: JP13.1, P4.2B (MOT-2B)
E-MS1: P4.MS1, SJ13.1
E-MS2: P4.MS2, SJ9.1
E-MS3: P4.MS3, SJ5.1
E-RESETSLEEP: P4.!RST (!RESET), P4.!SLP (!SLEEP)
E-STOP: JP10.1, U5.18 (PE4_INT4_TOSC1)
ENDSTOP+V: JP6.2, JP8.2, JP9.2, JP10.2
GND: C1.2, C2.2, C4.1, C5.1, C6.1, C7.2, C8.1, C9.2, C10.2, C11.-, C12.1, C13.1, C14.-, C15.1, C16.1, C17.-, C18.-, C19.-, C20.-, D1.A, D2.A, J1.1 (+), J1.2 (-), J2.1 (+), J2.2 (-), J3.1 (+), J3.2 (-), J4.1 (+), J4.2 (-), J5.1 (+), J5.2 (-), J6.1 (+), J6.2 (-), J7.1 (+), J7.2 (-), J8.2, J9.2, J10.6 (GND), J10.C1 (SHEILD), J10.C2 (SHIELD), J10.C3 (SHIELD), J10.C4 (SHIELD), J10.CD1, J11.GND, J11.GND1 (GND), J11.GND2 (GND), J11.GND3 (GND), J11.GND4 (GND), J11.GND5 (GND), J11.GND6 (GND), J11.GND7 (GND), J11.GND8 (GND), J13.3, J13.4, J15.4, J15.5, J15.6, J16.1, J18.2, J19.2, JP1.1, JP5.2, JP7.3, JP8.3, JP9.3, JP10.3, LED1.C, P1.GNDMOT, P1.GNDVDD, P2.GNDMOT, P2.GNDVDD, P3.GNDMOT, P3.GNDVDD, P4.GNDMOT, P4.GNDVDD, Q1.2 (S), Q2.1 (S1), Q2.2 (S2), Q2.3 (S3), Q3.2 (E), Q4.1 (S1), Q4.2 (S2), Q4.3 (S3), R2.2, R5.2, R8.2, R12.2, S1.1, S1.2, SCREW1.GND, SCREW2.GND, SCREW3.GND, SCREW4.GND, U1.2 (GND), U2.1 (GND), U3.3 (GND), U4.7 (GND), U5.6 (UGND), U5.22 (GND), U5.53 (GND), U5.63 (AGND)
HOTBED-GND: J17.1, J17.2, Q4.5-8 (D)
HOTEND-GND: J14.1, J14.2, Q2.5-8 (D)
MISO: JP1.6, U4.13 (B1), U5.13 (PB3_PDO_PCINT3_MISO)
MOSI: JP1.3, U4.11 (B3), U5.12 (PB2_PDI_PCINT2_MOSI)
unnamed: LED1.A, R1.1
unnamed: Q4.4 (G), R13.2
unnamed: R6.2, U5.4 (D-)
unnamed: R7.2, U5.5 (D+)
unnamed: F1.P$2, J12.2
unnamed: D1.C, F1.P$1, Q1.3 (D)
unnamed: Q1.1 (G), R3.2
unnamed: Q2.4 (G), R9.2
PB4: J16.5, U5.14 (PB4_PCINT4_OC2A)
PD0-SCL: J16.6, U5.25 (PD0_OC0B_SCL_INT0)
PD1-SDA: J16.7, U5.26 (PD1_OC2B_SDA_INT1)
PD2-RX1: J16.8, U5.27 (PD2_RXD1_INT2)
PD3-TX1: J16.9, U5.28 (PD3_TXD1_INT3)
PD4: J16.10, U5.29 (PD4_ICP1)
PD5: J16.11, U5.30 (PD5_XCK1)
PD6: J16.12, U5.31 (PD6_T1)
PD7: J16.13, U5.32 (PD7_T0)
PE3: U5.9 (PE3_IUID)
PE5: J16.4, U5.19 (PE5_INT5_TOSC2)
PE7: U5.2 (PE7_INT7_AIN1_UVCON)
SCLK: JP1.4, U4.12 (B2), U5.11 (PB1_PCINT1_SCLK)
SDCD: J10.CD2, U5.17 (PB7_PCINT7_OC0A_OC1C)
SDCLK: J10.5 (CLK), U4.3 (A2)
SDCS: U4.10 (B4), U5.10 (PB0_SS_PCINT0)
SDCSH: J10.2 (DAT3/CS), U4.5 (A4)
SDDI: J10.3 (CMD/DI), U4.4 (A3)
SDDO: J10.7 (DAT0/DO), U4.2 (A1)
UCAP: C8.2, U5.7 (UCAP)
USB_DN: J11.D-, R6.1, U2.3 (IO2)
USB_DP: J11.D+, R7.1, U2.2 (IO1)
VBUS: C4.2, J11.VBUS, SJ1.1, U2.4 (VCC), U5.3 (UVCC), U5.8 (VBUS)
X-DIR: P1.DIR, U5.49 (PA2_AD2)
X-MOT-1A: JP11.3, P1.1A (MOT-1A)
X-MOT-1B: JP11.4, P1.1B (MOT-1B)
X-MOT-2A: JP11.2, P1.2A (MOT-2A)
X-MOT-2B: JP11.1, P1.2B (MOT-2B)
X-MS1: P1.MS1, SJ10.1
X-MS2: P1.MS2, SJ6.1
X-MS3: P1.MS3, SJ2.1
X-RESETSLEEP: P1.!RST (!RESET), P1.!SLP (!SLEEP)
X-STEP: P1.STEP, U5.50 (PA1_AD1)
X-STOP: JP8.1, U5.16 (PB6_PCINT6_OC1B)
XTAL1: C13.2, U5.24 (XTAL1), X1.P$2 (2)
XTAL2: C12.2, U5.23 (XTAL2), X1.P$1 (1)
Y-DIR: P2.DIR, U5.46 (PA5_AD5)
Y-MOT-1A: JP12.3, P2.1A (MOT-1A)
Y-MOT-1B: JP12.4, P2.1B (MOT-1B)
Y-MOT-2A: JP12.2, P2.2A (MOT-2A)
Y-MOT-2B: JP12.1, P2.2B (MOT-2B)
Y-MS1: P2.MS1, SJ11.1
Y-MS2: P2.MS2, SJ7.1
Y-MS3: P2.MS3, SJ3.1
Y-RESETSLEEP: P2.!RST (!RESET), P2.!SLP (!SLEEP)
Y-STEP: P2.STEP, U5.47 (PA4_AD4)
Y-STOP: JP9.1, U5.15 (PB5_PCINT5_OC1A)
Z-DIR: P3.DIR, U5.42 (PC7_A15_IC3_CLK0)
Z-MOT-1A: JP14.3, P3.1A (MOT-1A)
Z-MOT-1B: JP14.4, P3.1B (MOT-1B)
Z-MOT-2A: JP14.2, P3.2A (MOT-2A)
Z-MOT-2B: JP14.1, P3.2B (MOT-2B)
Z-MS1: P3.MS1, SJ12.1
Z-MS2: P3.MS2, SJ8.1
Z-MS3: P3.MS3, SJ4.1
Z-RESETSLEEP: P3.!RST (!RESET), P3.!SLP (!SLEEP)
Z-STEP: P3.STEP, U5.44 (PA7_AD7)
Z-STOP: Q3.3 (C), U5.1 (PE6_INT6_AIN0)
Z-STOP-BIAS: JP7.1, Q3.1 (B)

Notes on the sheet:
Motor Control X
Motor Control Y
Motor Control Z
Motor Control E
ISP
Thermistors
Endstops
Mosfets
Power Acc
TeensyluV1
Rev 1.3a
Control for Reprap
Licensed under the Creative Commons Attributions ShareAlike 3.0 License
Extension Pin Headers
Power from ATX PS
5v Switching Regulator
SD and 3.3V Supply
*Note Stuff one connector or the other, not both.

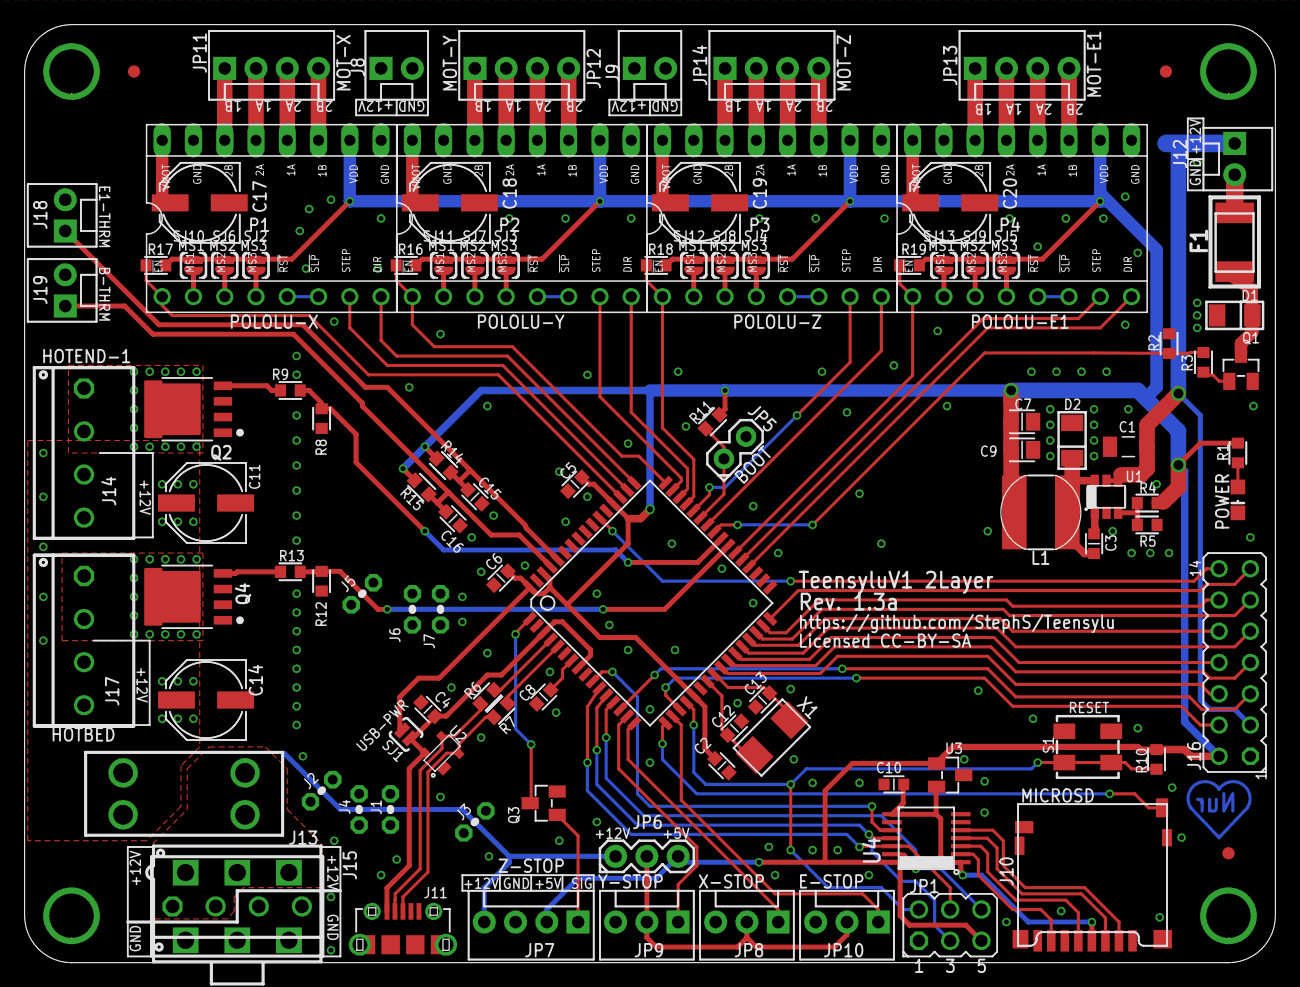
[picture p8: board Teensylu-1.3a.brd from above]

Board: 2 copper layers, 101.6 x 76.2 mm, 110 parts (0 on the bottom side), 101 nets.

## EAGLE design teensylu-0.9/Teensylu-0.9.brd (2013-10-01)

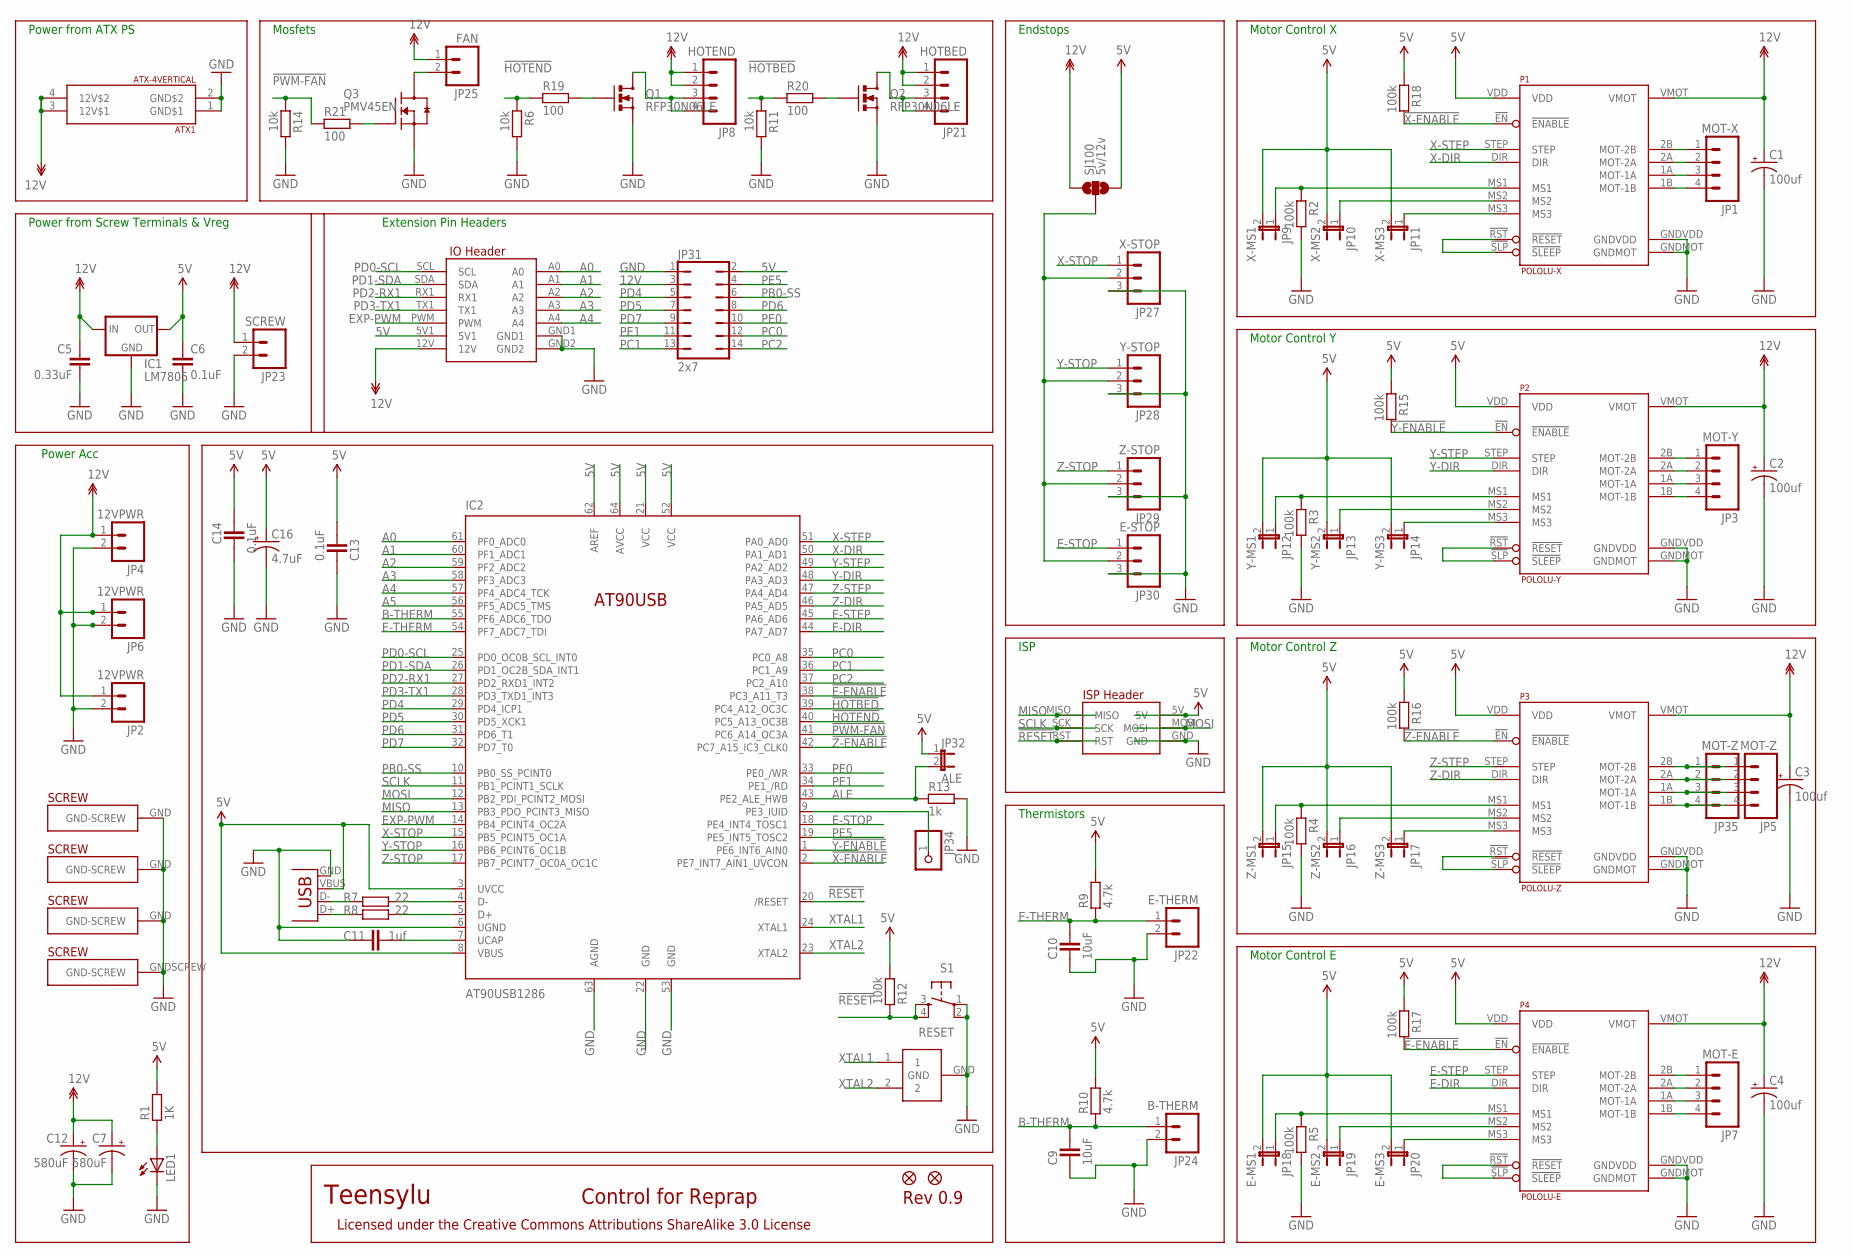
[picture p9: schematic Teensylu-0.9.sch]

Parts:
ATX1: ATX-4VERTICAL; MINIFITJR-4-VERTICAL
C1, C2, C3, C4: 100uf; CPOL-RADIAL-100UF-25V
C5: 0.33uF; CAP-PTH-SMALL2
C6: 0.1uF; CAP-PTH-SMALL2
C7, C12: 580uF; CPOL-RADIAL-1000UF-25V
C9, C10: 10uF; CAPC1608X92N
C11: 1uf; CAPC1608X92N
C13, C14: 0.1uF; CAPC1608X92N
C16: 4.7uF; CPOL-RADIAL-10UF-25V
IC1: LM7805; 78XXL-CUSTOM
IC2: AT90USB1286; TQFP64-2
J1: USB; USB-B-PTH
JP1: MOT-X; MOLEX-1X4
JP2, JP4, JP6: 12VPWR; MOLEX-1X2
JP3: MOT-Y; MOLEX-1X4
JP5, JP35: MOT-Z; MOLEX-1X4
JP7: MOT-E; MOLEX-1X4
JP8: HOTEND; MOLEX-1X4
JP9: X-MS1; 1X02
JP10: X-MS2; 1X02
JP11: X-MS3; 1X02
JP12: Y-MS1; 1X02
JP13: Y-MS2; 1X02
JP14: Y-MS3; 1X02
JP15: Z-MS1; 1X02
JP16: Z-MS2; 1X02
JP17: Z-MS3; 1X02
JP18: E-MS1; 1X02
JP19: E-MS2; 1X02
JP20: E-MS3; 1X02
JP21: HOTBED; MOLEX-1X4
JP22: E-THERM; 1X02
JP23: SCREW; SCREWTERMINAL-5MM-2
JP24: B-THERM; 1X02
JP25: FAN; 1X02
JP26, JP33: FIDUCIAL1X2.5; FIDUCIAL-1X2.5
JP27: X-STOP; MOLEX-1X3
JP28: Y-STOP; MOLEX-1X3
JP29: Z-STOP; MOLEX-1X3
JP30: E-STOP; MOLEX-1X3
JP31: 2x7; JP7Q
JP32: ALE; 1X02
JP34: PINHD-1X1; 1X01
LED1: LED5MM
P1: POLOLU-X; POLOLU-ALLEGRO-PTH
P2: POLOLU-Y; POLOLU-ALLEGRO-PTH
P3: POLOLU-Z; POLOLU-ALLEGRO-PTH
P4: POLOLU-E; POLOLU-ALLEGRO-PTH
Q1, Q2: RFP30N06LE; TO220V
Q3: PMV45EN; SOT95P280X135-3N
R1: 1K; RESC1608X55N
R2, R3, R4, R5, R12, R15, R16, R17, R18: 100k; RESC1608X55N
R6, R11, R14: 10k; RESC1608X55N
R7, R8: 22; RESC1608X55N
R9, R10: 4.7k; RESC1608X55N
R13: 1k; RESC1608X55N
R19, R20, R21: 100; RESC1608X55N
S1: RESET; TACTILE-PTH
SJ100: 5v/12v; SJ_2W
U$17, U$24, U$37: PLATED-SCREW; PLATEDSCREW
U$34: IO_HEADERS_SCREW; IO_HEADER-PLATEDSCREW
XTAL: KYOCERA_PQRC_TYPE_S_RESONATOR; AVX_3.2X1.3_RESONATOR

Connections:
5V: C6.1, C13.2, C14.1, C16.1 (+), IC1.OUT, IC2.3 (UVCC), IC2.8 (VBUS), IC2.21 (VCC), IC2.52 (VCC), IC2.62 (AREF), IC2.64 (AVCC), J1.VBUS, JP9.2, JP10.2, JP11.2, JP12.2, JP13.2, JP14.2, JP15.2, JP16.2, JP17.2, JP18.2, JP19.2, JP20.2, JP31.2, JP32.1, P1.VDD, P2.VDD, P3.VDD, P4.VDD, R1.2, R9.2, R10.2, R12.2, R15.1, R16.1, R17.1, R18.1, SJ100.3, U$34.5V, U$34.5V1
12V: ATX1.3 (12V$1), ATX1.4 (12V$2), C1.1 (+), C2.1 (+), C3.1 (+), C4.1 (+), C5.1, C7.1 (+), C12.1 (+), IC1.IN, JP2.1, JP4.1, JP6.1, JP8.1, JP8.2, JP21.1, JP21.2, JP23.1, JP25.1, JP31.3, P1.VMOT, P2.VMOT, P3.VMOT, P4.VMOT, SJ100.1, U$34.12V
!E-ENABLE: IC2.38 (PC3_A11_T3), P4.!EN (!ENABLE), R17.2
!HOTBED: IC2.39 (PC4_A12_OC3C), R11.1, R20.1
!HOTEND: IC2.40 (PC5_A13_OC3B), R6.1, R19.1
!PWM-FAN: IC2.41 (PC6_A14_OC3A), R14.1, R21.1
!RESET: IC2.20 (/RESET), R12.1, S1.3, S1.4, U$34.RST
!X-ENABLE: IC2.2 (PE7_INT7_AIN1_UVCON), P1.!EN (!ENABLE), R18.2
!Y-ENABLE: IC2.1 (PE6_INT6_AIN0), P2.!EN (!ENABLE), R15.2
!Z-ENABLE: IC2.42 (PC7_A15_IC3_CLK0), P3.!EN (!ENABLE), R16.2
A0: IC2.61 (PF0_ADC0), U$34.A0
A1: IC2.60 (PF1_ADC1), U$34.A1
A2: IC2.59 (PF2_ADC2), U$34.A2
A3: IC2.58 (PF3_ADC3), U$34.A3
A4: IC2.57 (PF4_ADC4_TCK), U$34.A4
A5: IC2.56 (PF5_ADC5_TMS)
ALE: IC2.43 (PE2_ALE_HWB), JP32.2, R13.1
B-THERM: C9.2, IC2.55 (PF6_ADC6_TDO), JP24.1, R10.1
E-DIR: IC2.44 (PA7_AD7), P4.DIR
E-MOT-1A: JP7.3, P4.1A (MOT-1A)
E-MOT-1B: JP7.4, P4.1B (MOT-1B)
E-MOT-2A: JP7.2, P4.2A (MOT-2A)
E-MOT-2B: JP7.1, P4.2B (MOT-2B)
E-MS1: JP18.1, P4.MS1, R5.1
E-MS2: JP19.1, P4.MS2
E-MS3: JP20.1, P4.MS3
E-RESETSLEEP: P4.!RST (!RESET), P4.!SLP (!SLEEP)
E-STEP: IC2.45 (PA6_AD6), P4.STEP
E-STOP: IC2.18 (PE4_INT4_TOSC1), JP30.1
E-THERM: C10.2, IC2.54 (PF7_ADC7_TDI), JP22.1, R9.1
ENDSTOP+V: JP27.2, JP28.2, JP29.2, JP30.2, SJ100.2
EXP-PWM: IC2.14 (PB4_PCINT4_OC2A), U$34.PWM
GND: ATX1.1 (GND$1), ATX1.2 (GND$2), C1.2 (-), C2.2 (-), C3.2 (-), C4.2 (-), C5.2, C6.2, C7.2 (-), C9.1, C10.1, C11.1, C12.2 (-), C13.1, C14.2, C16.2 (-), IC1.GND, IC2.6 (UGND), IC2.22 (GND), IC2.53 (GND), IC2.63 (AGND), J1.GND, JP2.2, JP4.2, JP6.2, JP22.2, JP23.2, JP24.2, JP27.3, JP28.3, JP29.3, JP30.3, JP31.1, LED1.K (C), P1.GNDMOT, P1.GNDVDD, P2.GNDMOT, P2.GNDVDD, P3.GNDMOT, P3.GNDVDD, P4.GNDMOT, P4.GNDVDD, Q1.3 (S), Q2.3 (S), Q3.2 (S), R2.2, R3.2, R4.2, R5.2, R6.2, R11.2, R13.2, R14.2, S1.1, S1.2, U$17.GND, U$24.GND, U$34.GND, U$34.GND1, U$34.GND2, U$34.GNDSCREW (GND-SCREW), U$37.GND, XTAL.GND
HOTBED-GND: JP21.3, JP21.4, Q2.2 (D)
HOTEND-GND: JP8.3, JP8.4, Q1.2 (D)
MISO: IC2.13 (PB3_PDO_PCINT3_MISO), U$34.MISO
MOSI: IC2.12 (PB2_PDI_PCINT2_MOSI), U$34.MOSI
unnamed: LED1.A, R1.1
unnamed: J1.D-, R7.1
unnamed: IC2.4 (D-), R7.2
unnamed: IC2.5 (D+), R8.2
unnamed: J1.D+, R8.1
unnamed: JP25.2, Q3.3 (D)
unnamed: IC2.9 (PE3_IUID), JP34.1
unnamed: C11.2, IC2.7 (UCAP)
unnamed: Q3.1 (G), R21.2
unnamed: Q1.1 (G), R19.2
unnamed: Q2.1 (G), R20.2
PB0-SS: IC2.10 (PB0_SS_PCINT0), JP31.6
PC0: IC2.35 (PC0_A8), JP31.12
PC1: IC2.36 (PC1_A9), JP31.13
PC2: IC2.37 (PC2_A10), JP31.14
PD0-SCL: IC2.25 (PD0_OC0B_SCL_INT0), U$34.SCL
PD1-SDA: IC2.26 (PD1_OC2B_SDA_INT1), U$34.SDA
PD2-RX1: IC2.27 (PD2_RXD1_INT2), U$34.RX1
PD3-TX1: IC2.28 (PD3_TXD1_INT3), U$34.TX1
PD4: IC2.29 (PD4_ICP1), JP31.5
PD5: IC2.30 (PD5_XCK1), JP31.7
PD6: IC2.31 (PD6_T1), JP31.8
PD7: IC2.32 (PD7_T0), JP31.9
PE0: IC2.33 (PE0_/WR), JP31.10
PE1: IC2.34 (PE1_/RD), JP31.11
PE5: IC2.19 (PE5_INT5_TOSC2), JP31.4
SCLK: IC2.11 (PB1_PCINT1_SCLK), U$34.SCK
X-DIR: IC2.50 (PA1_AD1), P1.DIR
X-MOT-1A: JP1.3, P1.1A (MOT-1A)
X-MOT-1B: JP1.4, P1.1B (MOT-1B)
X-MOT-2A: JP1.2, P1.2A (MOT-2A)
X-MOT-2B: JP1.1, P1.2B (MOT-2B)
X-MS1: JP9.1, P1.MS1, R2.1
X-MS2: JP10.1, P1.MS2
X-MS3: JP11.1, P1.MS3
X-RESETSLEEP: P1.!RST (!RESET), P1.!SLP (!SLEEP)
X-STEP: IC2.51 (PA0_AD0), P1.STEP
X-STOP: IC2.15 (PB5_PCINT5_OC1A), JP27.1
XTAL1: IC2.24 (XTAL1), XTAL.1
XTAL2: IC2.23 (XTAL2), XTAL.2
Y-DIR: IC2.48 (PA3_AD3), P2.DIR
Y-MOT-1A: JP3.3, P2.1A (MOT-1A)
Y-MOT-1B: JP3.4, P2.1B (MOT-1B)
Y-MOT-2A: JP3.2, P2.2A (MOT-2A)
Y-MOT-2B: JP3.1, P2.2B (MOT-2B)
Y-MS1: JP12.1, P2.MS1, R3.1
Y-MS2: JP13.1, P2.MS2
Y-MS3: JP14.1, P2.MS3
Y-RESETSLEEP: P2.!RST (!RESET), P2.!SLP (!SLEEP)
Y-STEP: IC2.49 (PA2_AD2), P2.STEP
Y-STOP: IC2.16 (PB6_PCINT6_OC1B), JP28.1
Z-DIR: IC2.46 (PA5_AD5), P3.DIR
Z-MOT-1A: JP5.3, JP35.3, P3.1A (MOT-1A)
Z-MOT-1B: JP5.4, JP35.4, P3.1B (MOT-1B)
Z-MOT-2A: JP5.2, JP35.2, P3.2A (MOT-2A)
Z-MOT-2B: JP5.1, JP35.1, P3.2B (MOT-2B)
Z-MS1: JP15.1, P3.MS1, R4.1
Z-MS2: JP16.1, P3.MS2
Z-MS3: JP17.1, P3.MS3
Z-RESETSLEEP: P3.!RST (!RESET), P3.!SLP (!SLEEP)
Z-STEP: IC2.47 (PA4_AD4), P3.STEP
Z-STOP: IC2.17 (PB7_PCINT7_OC0A_OC1C), JP29.1

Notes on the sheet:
Motor Control X
Motor Control Y
Motor Control Z
Motor Control E
ISP
Thermistors
Endstops
Mosfets
Power Acc
Teensylu
Rev 0.9
Control for Reprap
Licensed under the Creative Commons Attributions ShareAlike 3.0 License
Extension Pin Headers
Power from ATX PS
Power from Screw Terminals & Vreg

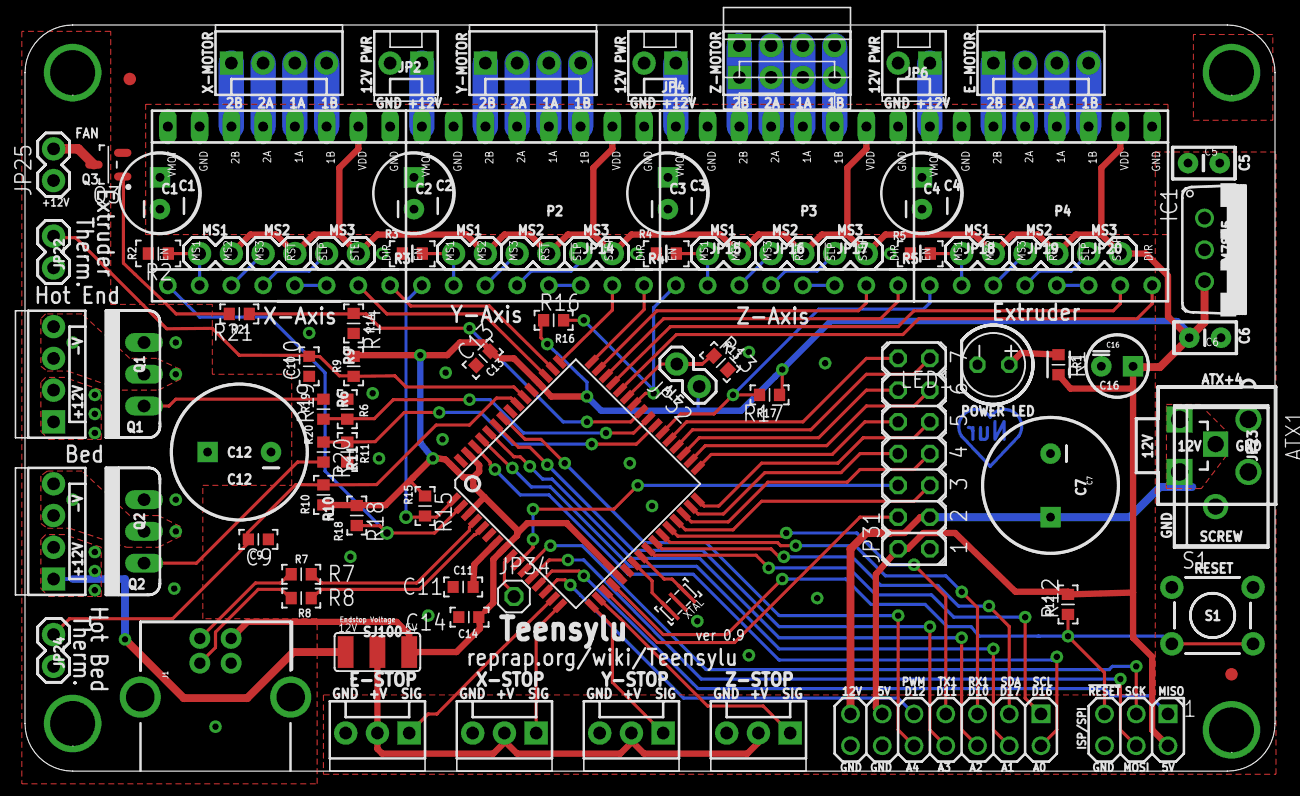
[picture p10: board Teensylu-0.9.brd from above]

Board: 2 copper layers, 100.0 x 59.7 mm, 89 parts (0 on the bottom side), 98 nets.

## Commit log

2011-04-28 Checking in lost files.
    [Teensylu-0.1.brd, Teensylu-0.1.sch, Teensylu-0.2.brd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]
2011-04-30 Lots of changes. Added Enable Pin to each motor controller, Extra I/O header is now reduced to 7x2 header. Cleaned up routing. Moved 4.7uF cap to 5v Input (Value may change). Added pullup jumper to A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
    [Teensylu-0.4.3.brd, Teensylu-0.4.3.sch]
2011-05-01 Added Version number to silkscreen.
    [Teensylu-0.4.3.brd, Teensylu-0.4.3.sch, Teensylu.brd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]
2011-05-01 create 0.5 revision folder with images and gerbers
    [Teensylu-0.5.brd, Teensylu-0.5.sch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]
2011-05-01 updated working
    [Teensylu.sch]
2011-05-01 Swapped pins to add PWM to expansion header.
    [Teensylu-0.6.brd, Teensylu-0.6.sch]
2011-05-02 Updating working folder.
    [Teensylu.brd, Teensylu.sch]
2011-05-08 Adding a BOM for the current working version and v0.6
2011-05-08 Changing caps to 35v
2011-05-08 Cleaned up the BOM some more. TODO: Seperate optional components.
2011-06-25 Added C7, changed C12 capacitance to 580uF to reduce physical dimensions. Changed Expansion header to match sanguinololu rev 1.2 expansion header. Changed package of MCU to meet specs for better sold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
    [Teensylu-0.7.brd, Teensylu-0.7.sch]
2011-06-25 Updated working to rev 0.7
    [Teensylu.brd, Teensylu.sch]
2011-06-30 R13 changed to 10k. Smaller BOM, save in bulk.
2011-11-03 Added 4 new 100k resistors to pullup stepper motor enable pins during programming. Also added second header for Z motor output (Prusa Mendel Friendly!). Still needs some minor tweaking to silkscreen 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
    [Teensylu-0.8.brd, Teensylu-0.8.sch]
2013-10-01 Added 100 ohm resistors to Mosfets. Changed ALL SMD components to 0603.
    I added a 100 ohm resistor to the gate of every mosfet. this should help
    prevent damage to the MCU.
    I changed all of the SMD components to 0603. I've been wanting to do
    this for a while. They're not much smaller than 0805, but it allows me
    to route things better.
    [Teensylu-0.9.brd, Teensylu-0.9.sch]
2014-06-02 Added warning
    Recommending the Teensylu not to be used until changes and modifications
    are made. This is based on the risk of damage or fire! Either do not use
    the board or take proper precautions!
    There is no such thing as a "Safe" 3d printer controller. Keep a smoke
    detector nearby and have a fire extinguisher handy. Do NOT leave
    unattended.
2015-05-18 New TeensyluV1
    The TeensyluV1 is a redesign of the Teensylu board. I have backported
    many of the features of the Teensylu2 board, and added new features like
    a blade fuse. I highly recommend using the V1 over the original Teensylu
    board.
    [Teensylu-1.0.brd, Teensylu-1.0.sch, Teensylu.brd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]
2015-07-10 Fixed Z endstop
    Collector and emitter pins were swapped.
    [Teensylu-1.1.brd, Teensylu-1.1.sch]
2015-08-25 Now with 4 layers!
    The board is now 4 layers. This is to allow high current through the
    planes. It also means less via's.
    [Teensylu-1.2.brd, Teensylu-1.2.sch]
2015-09-03 Adding 2 Layer board
    I decided that a 2 Layer board would be a cost effective option. I
    pulled the last 2 Layer board and cleaned it up.
    [Teensylu-1.2-4L.brd, Teensylu-1.2-4L.sch, Teensylu-1.2.brd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]
2015-09-14 Updated USB Diode, Added Jumper Wires, Z Endstop is now 4 pin
    The USB Diode has been changed to DRTR5V0U2SR
    22ga jumper wires added to increase current capacity
    Z Endstop header is now 4 pin. All future versions will use 4 pin
    endstop on Z. See schematics and set the appropriate pinout for your
    configuration.
    [Teensylu-1.2.sch, Teensylu-1.3.brd, Teensylu-1.3.sch]
2015-09-16 Updated heater mosfets
    I updated the heater mosfets to 40v version, part # PSMN1R8-40YLC,115
    [Teensylu-1.3a.brd, Teensylu-1.3a.sch]
2015-09-16 minor routing changes
    just a few changes to clean up routing.
    [Teensylu-1.3a.brd]
2015-11-09 Added dimensions
    Dimensions are added to make it easier to make enclosures.
    [Teensylu-1.3a.brd]

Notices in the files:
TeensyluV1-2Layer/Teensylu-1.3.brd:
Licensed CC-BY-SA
